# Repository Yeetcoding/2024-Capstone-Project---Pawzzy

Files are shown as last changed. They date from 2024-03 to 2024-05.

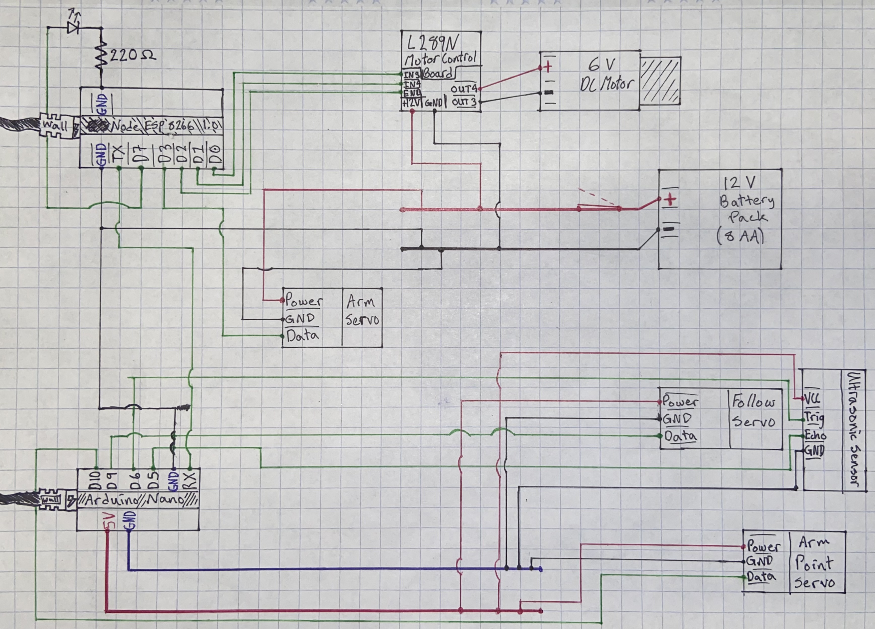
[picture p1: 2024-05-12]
Pawzzy--FINAL_Schematic.jpg

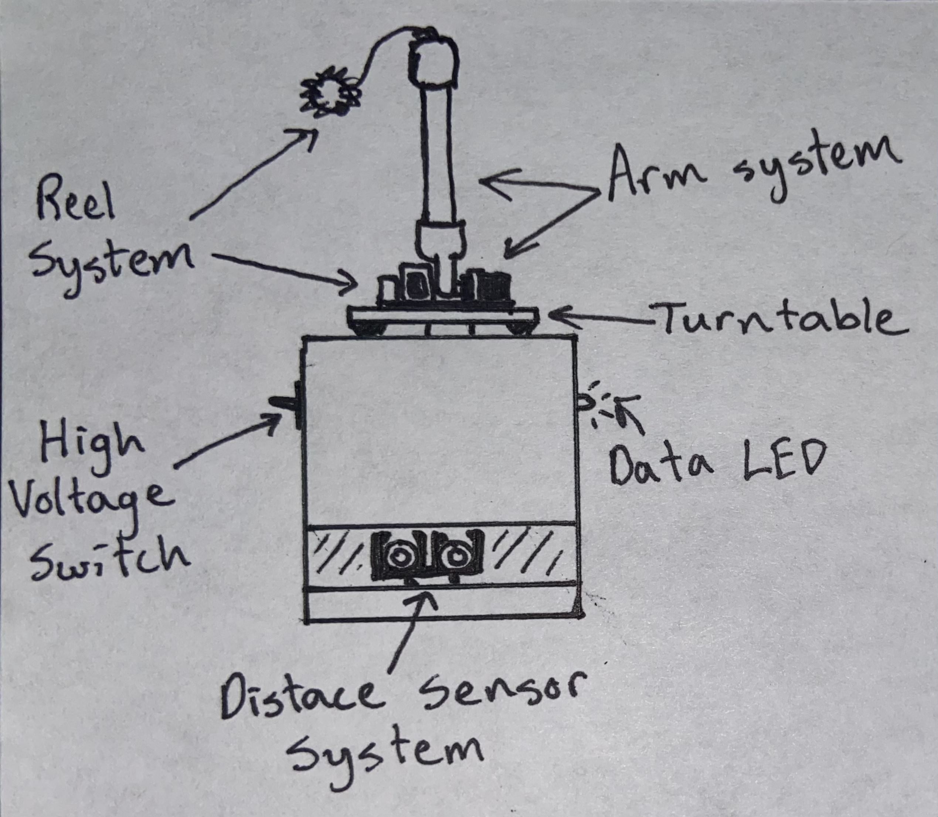
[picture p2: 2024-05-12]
Final_Drawing_Overveiw.jpg

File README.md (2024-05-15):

**2024 Capstone Project**

# **PAWZZY**

2024_05_15_11_23_IMG_0230

**By Chase Smith and Lincoln Willison**

May 15th, 2024

### Project Overview

This robot, named *Pawzzy*, is meant to entertain your cat while you, the owner, are away. One simple tap on your phone, and you don't have to worry about your cat 
feeling lonely! As you would with a cat toy, this machine takes a toy on a string, launches it, and then moves it around for the cat to try to catch. 

As shown in fig.1, the robot has a launch arm, where the toy is attached to moving reel. Like a fishing rod, this arm rotates forward very fast, and the reel is turned on so that the 
toy is launched at a desired distance. 

2024_05_15_11_21_IMG_0229

*Fig. 1*

Then the toy is slowly reeled in as the arm is moved around on the rotating plate, shown in fig.2.

2024_05_15_11_21_IMG_0228

*Fig. 2*

As the toy is being reeled in, the Ultrasonic Sensor at the bottom of the box shown in fig.3 moves close to the direction of the toy, so that if the cat gets close the toy can react and make 
it harder for the cat.

2024_05_15_11_21_IMG_0227

*Fig. 3*

### System Details

The Robot consists of 2 main systems, the Throwing System and a Detection System. As shown in fig.4, the Throwing System consists of the Arm System, The Reel System, and the Turntable, while the Detection System consists of the Distance Sensor and the Servo with it. The Throwing System is responsable for throwing, reeling in, and moving the cat toy, whereas the Detetion System is responsible for detecting the cat and initiating an appropriate response to with the rest of the machine.

Final_Drawing_Overveiw
*Fig.4*

The software for the project is written in Arduino C++, and it used with 2 microcrontrollers, the Node ESP-8266 1.0 and the Arduino Nano. The ESP is used to receive signals from the phone controller of the user and activate the system, as well as control the arm. Fig.5 shows the process and logic implimented in the ESP. 

Pawzzy_FlowC_Transm

*Fig.5*

The Nano is in charge of intaking data from the Detection system and moving the sensor and arm point in the right direction, to help avoid the cat and moce the toy around. Fig.6 shows the process and logic implimented in the Nano, as well as how it makes decisions based on input.

Pawzzy_FlowC_Receiver

*Fig.6*

The Arm Servo is connected to the ESP for control and the 12V battery for power. The Reel Motor is connected to the L289N Motor Control Board, which is controlled by the ESP and is powered by the 12V battery. The LED is connected to the ESP to show the received "ON" signal. The Distance Sensor, Arm Point servo, and Sensor servo are all controlled and powered by the Arduino Nano. Both boards are powered by power cables that plug into an extension cable, which plugs striaght into the wall. The two boards share a Serial connection over the ESP's TX (1) pin, the Nano's RX (0) pin, and a shared ground. All of the electronic wiring is shown on fig. 7. 



*Fig.7*

### Design Evaluation

**Overall Evaluation**

Pawzzy was made to solve two problems: Cat boredom, and the guilt the owner feels when they know their cat has had nothing to do while they're gone. To fufill this goal, we had to make a robot that would be reliable both locally with the randomness of the cat and with the distance of the owner. Our robot has many traits that make it reliable, fun, and beneficial for everyone invovled. We made the robot chassis out of wood to give it a stable and study base. We gave it rubber feet for maximum stability, grip, turn resistence, and so it doesn't scratch any surfaces it is on. We gave it a light blue color of paint to make it visually appealing but also non-threatening. We rounded out the edges of the robot and smoothed over rough surfaces, so that it couldn't hurt anyone or anything brushing against it. Lastly, we use a simply ON/OFF control system for the user, so that the user is only encountered with simplicity and fun times, while the robot does all the hard work. Blynk is a reliable and trusted service that works very fast and reliably, and is very user friendly. 

**Output Display**

For the category Output Display, Pawzzy uses a single LED on the side of the frame to indicate when the robot has received the user's input, as shown in Fig.8. This allows for more understanding of the robot's status to the human, as the human knows that the robot has received the signal to activate. The L298N Motor controller also has an LED to display when power is turned on, but this is hidden from the human since the board is inside the box. 

< insert Fig.8 (LED) here >
*Fig.8*

**Manual User Input**

For the category Manual User Input, Pawzzy uses two different types of input: One through Blynk (shown in Fig.9), where the user presses a digital button to activate the robot, and the other being a physical toggle switch on the side of the frame for controlling the 12V battery. The Blynk input is truly amazing as it allows the user to activate the machine from anywhere with an internet connection, which is perfect for when you are traveling and are away from your cat. At the airport, and want to make sure your cat is not bored? Simply go onto your phone, pressed the "ON" button, and forget about your worries.

< insert Fig.9 (Blynk Screenshots) here >
*Fig.9*
< insert Fig.10 (Toggle Switch) here >
*Fig.10*

**Automatic Sensor**

For the category Automatic Senor, Pawzzy uses an Ultrasonic Sensor, as shown in Fig.11. When combined with a rotating servo, this sensor gives the robot a sense of if the cat is close to the toy. This sensor senses distance, which we use to detect if the cat is close to the toy by closely aligning the senor and the toy. Using this input, the robot is able to move the toy away from the cat by itself, thereby making it harder and more engaging for the cat, as well as introducing more variables to make the moving process more random. 

< insert Fig.11 (Ultrasonic Sensor) here >

**Actuators, Mechanisms, & Hardware**

For the category Actuators, Mechanisms, & Hardware, Pawzzy uses a total of 3 servos and one DC motor, which are all shown in Fig.12. These motors move the arm, move the ultrasonic sensor, and point the arm in the right direction. Each of these motors are aligned and placed so that they fufill their task accordingly, give precise positions, and are not moved under pressure. We use 3d prints for housing and placement, and we use wood for builds like the arm and the box that will be placed under stress, giving it a custom and fitting but rigid design. 

< insert Fig.12 (Servos and Motors) >

**Logic, Processing, and Control**

For the category Logic, Processing, and Control, Pawzzy uses a total of 3 boards, 2 with code in Arduino C++, 1 for controlling power and the DC motor: The Node ESP 8266 1.0, the Arduino Nano, and the L289N, all of which are shown in Fig.13. Since Pawzzy is taking in a contant intake through the ultrasonic sensor and Blynk, it is important that the workload be split between 2 boards, so that one does not get clogged with data and that latency does not get in the way of executing crucial functions at certain times. Our boards are still able to communicate fast and efficiently through the Serial communication pins, where the position for the arm and the Ultrasonic Sensor is dicated by the ESP and received by the Nano, and all systems are able to use data from the others. Because of this two board system, we are able to use the constant input of the Ultrasonic Sensor to react quickly if there is a cat near the toy. The third board, the L289N, allows for us to draw power from a battery that we wouldn't have gotten from the nano or ESP themselves. 

< insert Fig.13 (Boards) >

**Additonal Adjustments**

When designing this, we made sure to do some thinking about how we would put everything together, instead of just throwing it all into a box. We use wood to make a rigid structure, and sand down the edges to make a good and quality feel. We soldered all of the wire joints and components together, so that the internal structure would have a reliable electrical system. We also put thought into the color of our paint - when researching a color that cats like, we found that blue was a common one. We picked our robot to have that blue for its inviting and friendly appeal, so that it would look good to the cat but also the human. We also made sure that the structure and construction of this project would ensure that the different components would work together flawlessly, which it does, as no wires get in the way of the sensor or turntable, and each moving part moves freely without any unecessary friction, and has the suppor that it needs to remain reliable. We are also able to make all of this at a reasonable price, and have no issues with running too close to the budget limit.

Because of the above reasons, we believe we qualify for these additives:
  - +10% for Construction, Quality, Aestetics, and Visual Appeal
  - +10% for Level of Effort
  - +10% for Construction/Production Cost

### Parts List
- Hongwang018 - Acrylic Disk, B0CC83YLVT, $4.50
- MG 996R Servo (x3), $13.50
- Node - ESP 8266 1.0, $5.00
- Arduino Nano, $6.5
- BOJACK - L289N Motor Controller, $3.00
- AEDIKO - DC Motor, $1.40
- Gikfun - Solder Board (x2), $4.4
- Door Hinge, $1.16
- QTEATAK - 8 AA Battery Pack, $3.50
- Plywood, $10
- Marble (x3), $0.30
- EPLZON - Ultrasonic Sensor HC-SR04, $2.00
- Power Strip, $5
- Ace Hardware - Blue paint, $1.8, 
- Ace Hardware - Dowel, $2

### Lessons Learned

- **Beware of the data input from the Ultrasonic Sensor**: During both of our previous capstone projects, we learned how constantly using ultrasonic sensors in a project bog down the time efficiency of the microcontrollers, so we made sure to institute a system that would be able to handle this situation.
- **You can speed up motors with a higher power source but still control it with a microcontroller**: When trying to make the arm servo go faster in order to launch the toy, Chase figured out that if you connect the ground of the Arduino and Power source together and attach the servo's data pin to the Arduino, you can control the servo but it will go significantly faster.
- **Plan out your work schedule and what you are going to make ahead of time**: Both of us have benefited from planning ahead of time what each of us will do with the time we have. In each of our own previous capstone projects, neiter of us planned ahead and barely got work done in time, but this year we were able to work efficiently both as a tem and as individuals because of our planning.
- **Take things step by step**: A concept that is often reiterated throughout all of engineering, it applies also to our situation. The software itself is complex and can get very confusing, so taking it step by step deliberately (especially the very small steps, such as simple Serial communication over a wire or hooking up a servo by itself) and not rushing ahead really helped to make sure all of the "foundations" were sound.
- **Pick a nice color of paint. Make it look 'perty**: Something that we both liked is how well our project looked when we finshed, especially after we put serious thought and effort into what we'd like it to look like. Making it look better, regardless of functionality (but not at the cost of), made us appriciate it more and make it look more friendly and awesome. This was a big difference from our past projects, as our previous projects looked more 'thrown' together than 'put' together.
- **Help others when you can**: Working in a robotics classroom environment like the one in Windosr helps you be around many different people with the same mindset, which means you can have many different opportunities to learn outside/other than the typical lecture to assignment structure. Being able to help others gives you a break from working on your project, gives you a look at other cool projects, and helps you form connections that might pay off later. After all, we know that we appreiciate a helping hand, so why not be that helping hand for another when you can?
- **Don't be a wimp - find a good partner**: Having a good partner changes the game with these capstone projects, as you can get a second view on the project instanly but you can also split the workload with your other partner. Even if you think you can do great yourself, you can do double with a good partner. Both of us chose to go solo with our previous projects, and work together for this one, and the difference is huge because both of us put pour best foot forward and worked hard together. Having a partner is definitely the best choice if you can find a good one. 

### Building Instructions

**If for some reason you've read through all of this and decided you want a crack at making Pawzzy, here are some simple steps to guide you along the way:**
1. Gather Supplies and Parts (parts listed above)
2. Put the Arm Point Servo in the middle of the lid, add on the acrylic cirlce and place all of the top components on the cirlce
3. Wrap all wires in electrical tape, then feed all wires from the top components through the holes in the back of the circle and lid
4. Once all wires are pulled through, solder everything to the appropriate breadboard
5. Attach all physical holders, such as the top assemblies that hold the motors or the dowel ends or the Ultrasonic sensor holder
6. Hot glue all boards and stationary platforms within (but not on the top of) the box to edges of the box
7. Drill 2 holes in opposite sides of the box, one bigger and one smaller
8. Place the High Voltage switch into the bigger of the drilled holes and screw in
9. Glue the LED into the smaller hole 
10. Close the lid of the box, and screw in all top components
11. String through the fishing line and attatch the toy to the end of the line, making sure to pass through all of the loops on the arm
12. Close the box and make sure everything closes fine

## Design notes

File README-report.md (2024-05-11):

**2024 Capstone Project**

# **PAWZZY**

< insert title photo here >

**By Chase Smith and Lincoln Willison**

### Project Overview

This robot, named *Pawzzy*, is meant to entertain your cat while you, the owner, are away. One simple tap on your phone, and you don't have to worry about your cat 
feeling lonely! As you would with a cat toy, this machine takes a toy on a string, launches it, and then moves it around for the cat to try to catch. 

As shown in fig.1, the robot has a launch arm, where the toy is attached to moving reel. Like a fishing rod, this arm rotates forward very fast, and the reel is turned on so that the 
toy is launched at a desired distance. 

< insert fig.1 (launch arm) here >

Then the toy is slowly reeled in as the arm is moved around on the rotating plate, shown in fig.2.

< insert fig.2 (rotating plate) here >

As the toy is being reeled in, the Ultrasonic Sensor at the bottom of the box shown in fig.3 moves close to the direction of the toy, so that if the cat gets close the toy can react and make 
it harder for the cat.

< insert fig.3 (Ultrasonic Sensor) here >

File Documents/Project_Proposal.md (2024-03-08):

2024-Capstone-Project---Pawzzy

Pawzzy

titleImagePawzzy

By Lincoln Willison and Chase Smith

Overview

Pawzzy will be an automated cat entertainment system, designed to eliminate your cat’s boredom while you are gone. The system timing will be determined based on a simple user input in the form of a timer. Once the desired time set by the human is reached, the cat toys will activate. 
	Pawzzy will consist of 4 different systems, The Arm toy, the Laser, the Obstacle Detection System, and the Treat Dispenser, each working together to entice and entertain the cat. The central box, where all of the components will be housed, will be made of either wood, cardboard, or foam with weights on the bottom so that it won't move around during its session.  

Fig 1
fig1_Pawzzy

The Arm Toy will be the main attraction, as it will control the toy that the cat chases. It will be rotated on 2 axes controlled each by a servo motor, so it could move up, down, left, and right, as shown in Fig 2. There will also be a reel controlled by a motor to control the reach of the toy, also shown in Fig 2. This reel will work in function with the arm to cast out the toy like a fishing line, then reel the toy in as the code dictates. The reel motor will also have an encoder, so that when the reel cannot reel in the toy if the cat captures the toy, the Arduino will know and can make decisions based off of that. 

Fig 2
fig2-Pawzzy

The Laser will be a separate system that is also controlled by two servos. The laser will be mounted on the two servos and point to various spots on the ground, as shown in Fig 3.

Fig 3
fig3-Pawzzy

The Obstacle detection system will be composed of an ultrasonic sensor and a servo. The servo will move the sensor in a semicircle, and the data collected from the sensor will be inputted into the Arduino. We have not yet determined where the sensor will be on the body, as the answer is better decided on testing.
The Treat Dispenser will dispense treats based on what happens to the toy, and how many treats the cat has already gotten. It will be controlled by a servo.  

Fig 4
fig4-Pawzzy

Components:

________________________________
Key:
Red: Output Display
Blue: Manual User Input
Orange: Automatic Sensor
Green: Actuators, Mechanisms and Hardware
Yellow: Logic, Processing, and Control
_____________________________________

Arduino Mega - to provide and execute the code of the project
Laser Diode - to make a laser that the cat chases
Wood/foam/cardboard - for the structure of the box
3d Print Filament - for the arm, spool, internal and external structure
6 small servo motors - 2 for the Arm, 2 for the laser, one for the distance sensor, and 1 for the treat dispenser
Small DC motor with encoder - for controlling the string attached to the arm and knowing when the cat has captured the toy
Buttons - for time input and input from the cat
LED’s - indicators for the working status of the machine, mode, and if toy has been captured
Ultrasonic Sensor - for sensing objects that might obstruct the toy throws
Buzzer - to signal accepted inputs (ei. Timer button pressed), signaling the capture of the toy, and the dispense of a treat

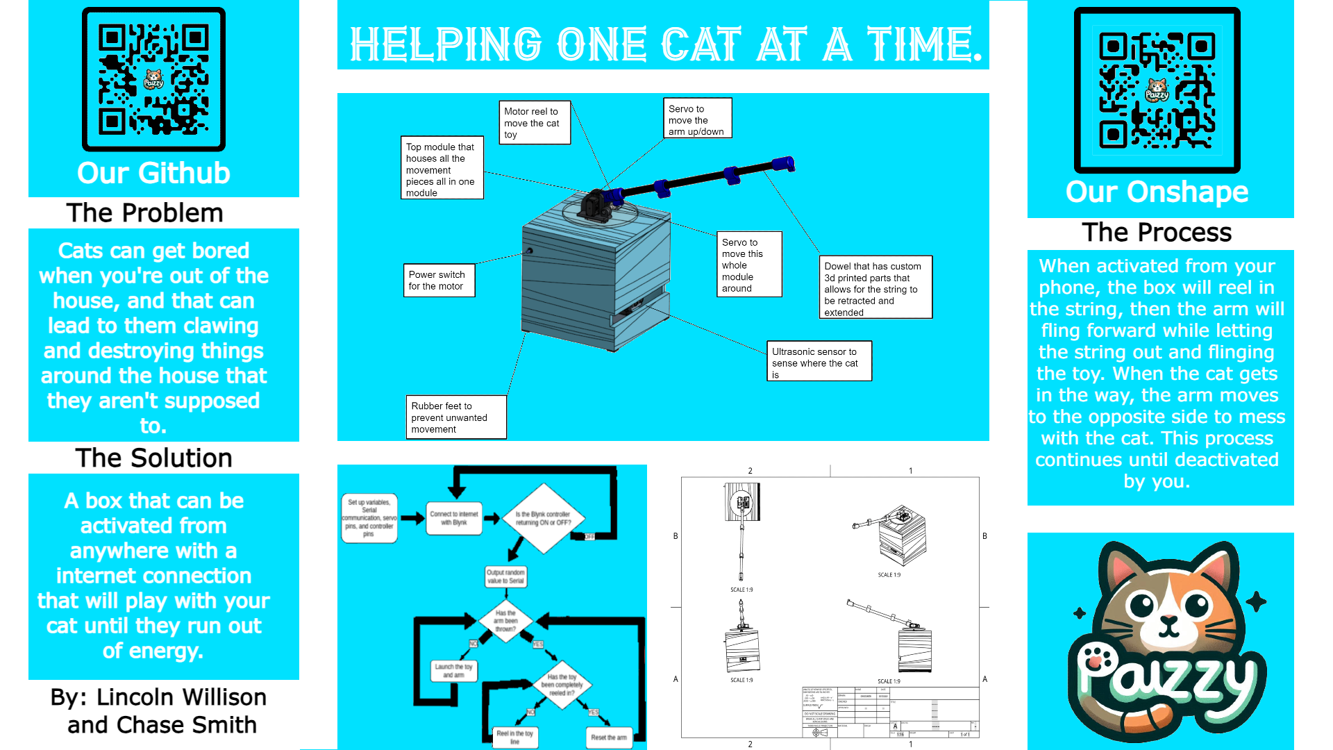
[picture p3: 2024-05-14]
Pawzzy_Poster.png

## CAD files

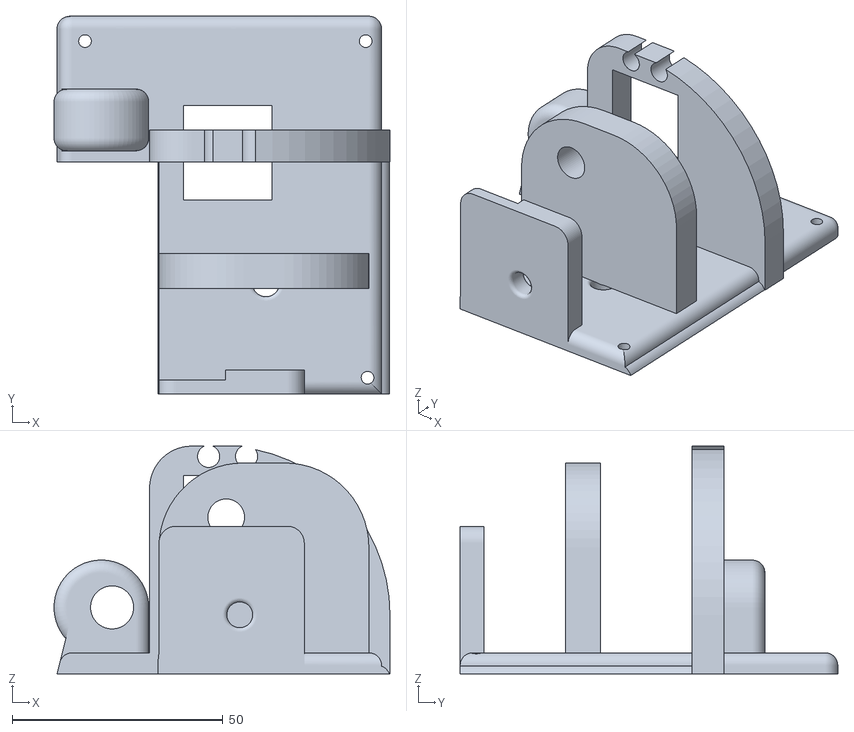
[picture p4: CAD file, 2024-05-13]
3D_Files/Top module (5).stl
79.7 x 89.5 x 54.0

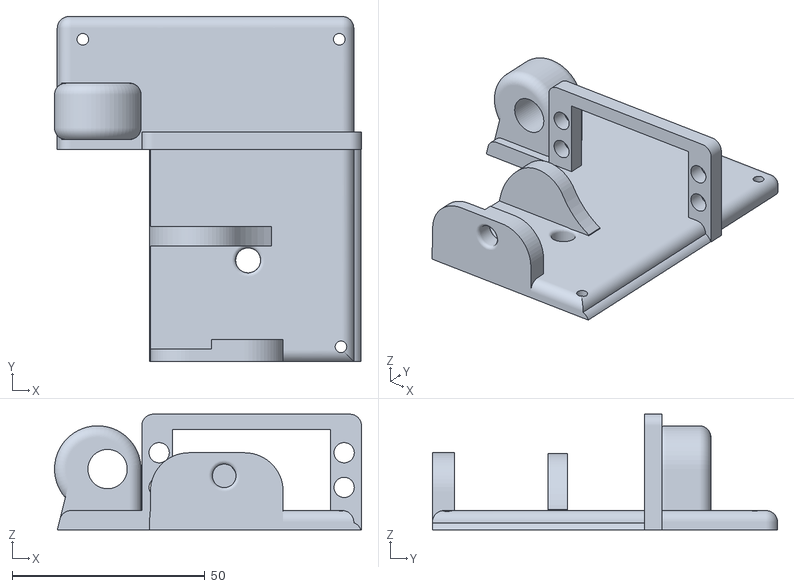
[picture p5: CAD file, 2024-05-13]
3D_Files/Top module (3).stl
79.7 x 89.5 x 30.0

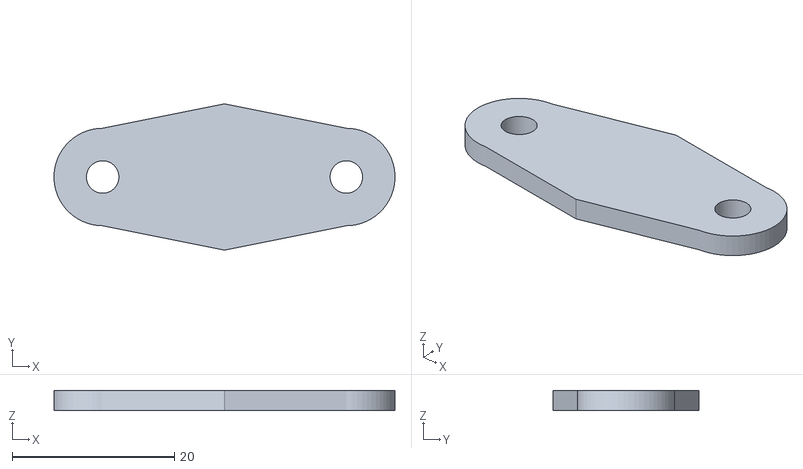
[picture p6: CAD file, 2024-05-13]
3D_Files/Marble roller spacer (2).stl
42.0 x 18.0 x 2.50

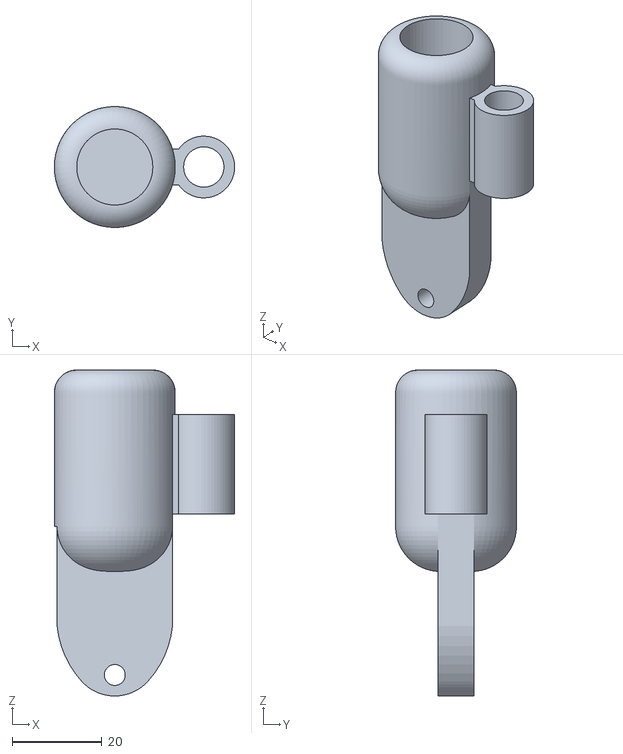
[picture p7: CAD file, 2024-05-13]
3D_Files/Dowel end (2).stl
40.3 x 27.0 x 72.8

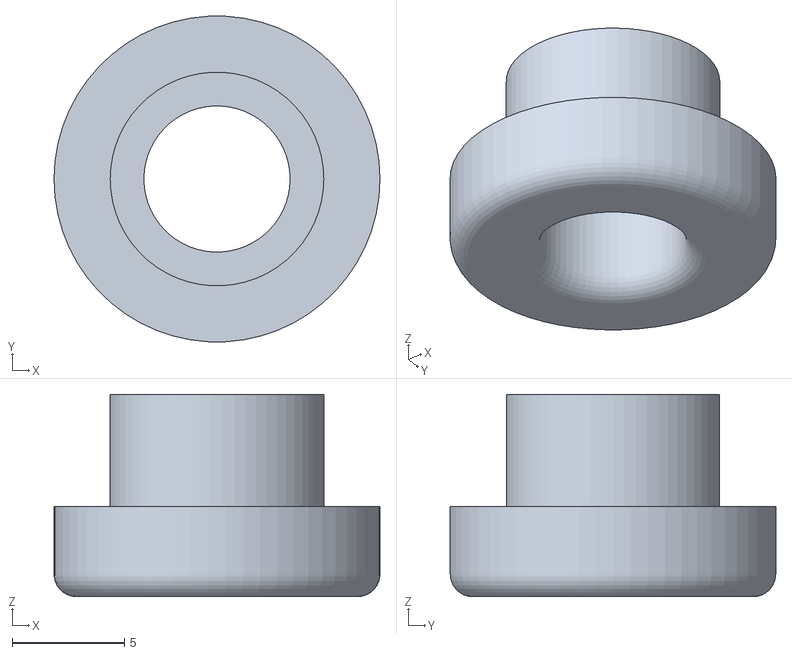
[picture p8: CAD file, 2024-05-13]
3D_Files/Cable insert (3).stl
14.5 x 14.5 x 9.00

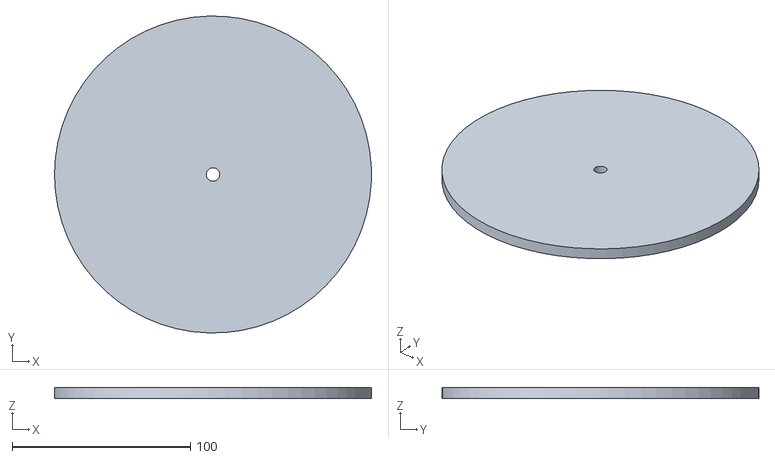
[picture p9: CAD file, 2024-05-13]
3D_Files/Turn table (1).stl
177.8 x 177.7 x 6.35

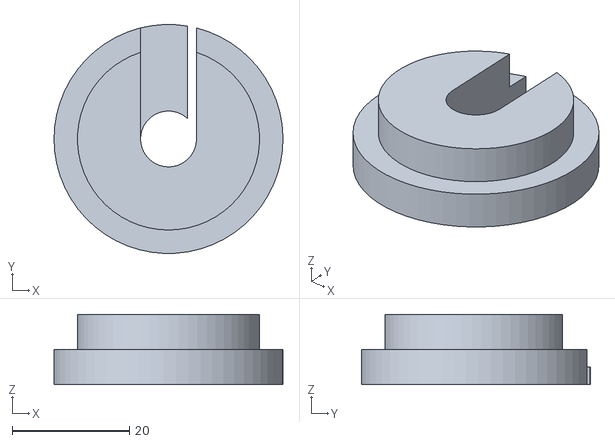
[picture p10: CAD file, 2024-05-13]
3D_Files/Power cord cover.stl
39.0 x 39.0 x 12.0

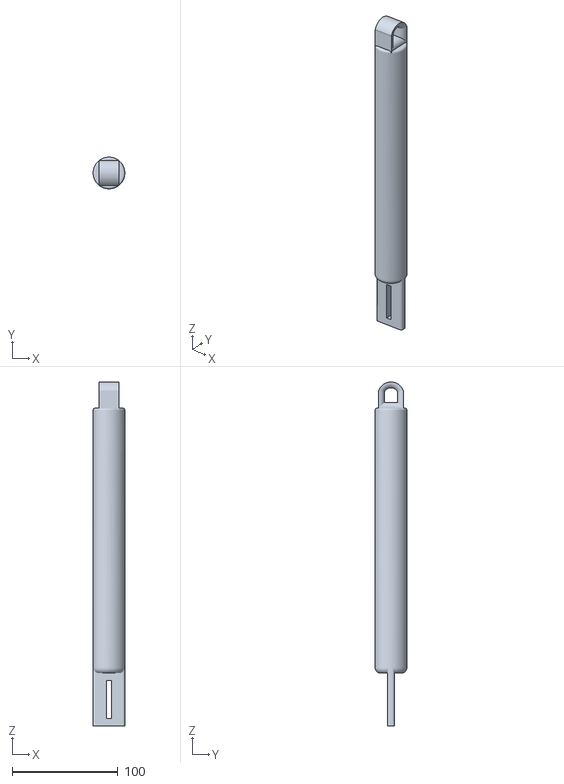
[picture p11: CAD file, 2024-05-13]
3D_Files/Throwing arm.stl
30.0 x 30.0 x 324.6

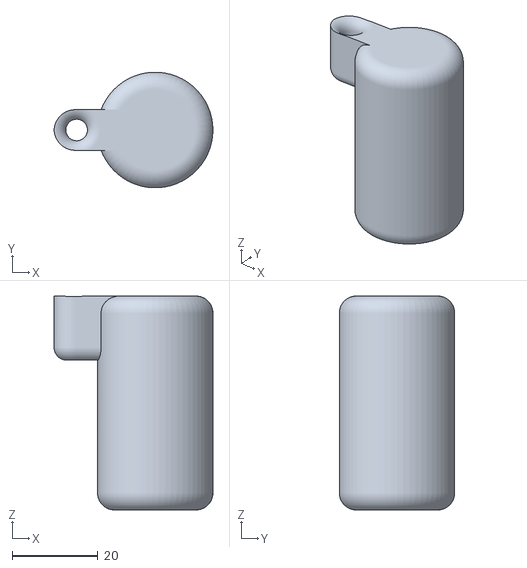
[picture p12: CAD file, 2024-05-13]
3D_Files/Other dowel end (1).stl
37.1 x 27.0 x 50.0

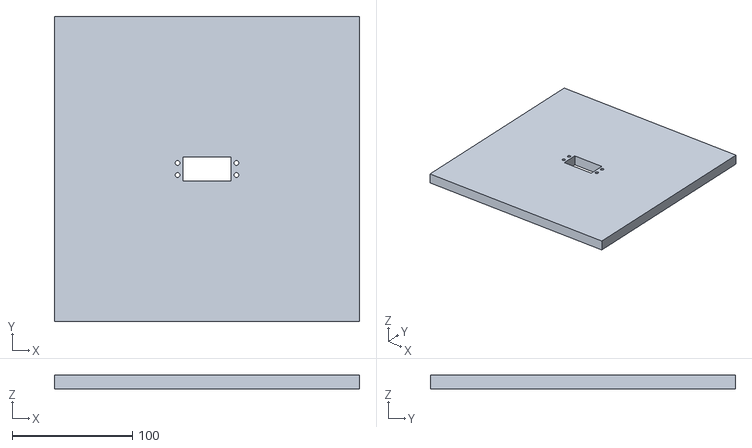
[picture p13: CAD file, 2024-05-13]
3D_Files/Lid.stl
254.0 x 254.0 x 12.0

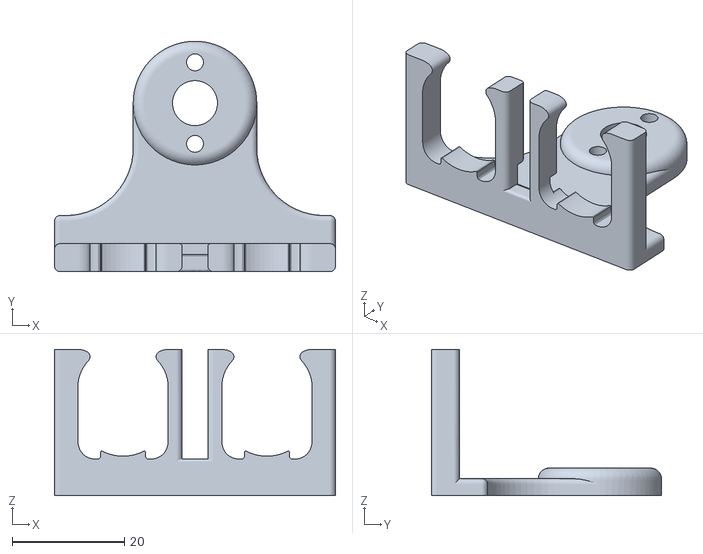
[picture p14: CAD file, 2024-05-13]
3D_Files/Ultra-sonic sensor holder (2).stl
50.0 x 41.0 x 26.0

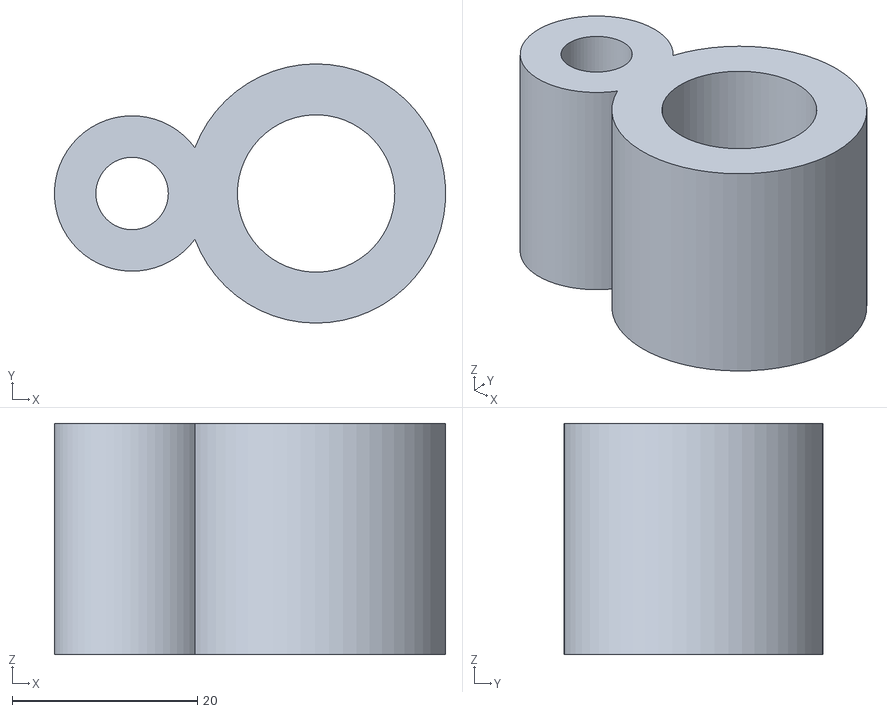
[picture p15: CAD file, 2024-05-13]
3D_Files/String retainer (1).stl
42.2 x 28.0 x 25.0

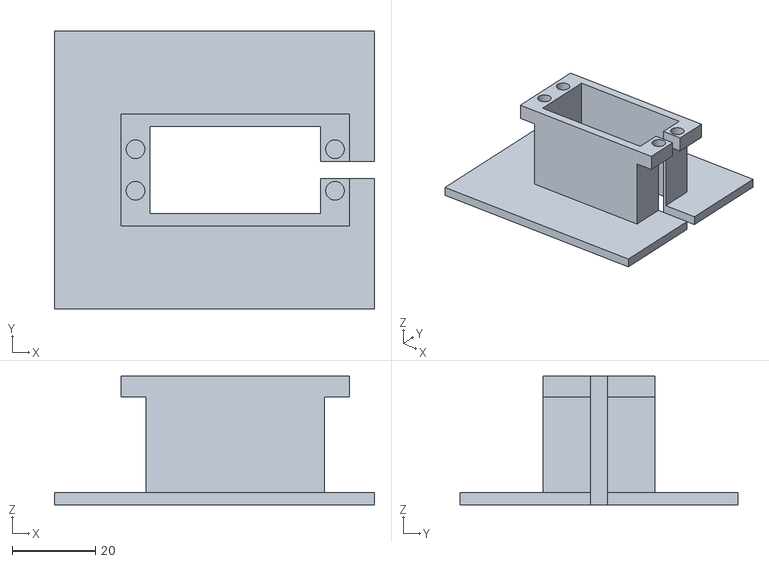
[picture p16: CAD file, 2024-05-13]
3D_Files/Ultrasonic sensor servo mount (2).stl
77.0 x 67.0 x 31.0

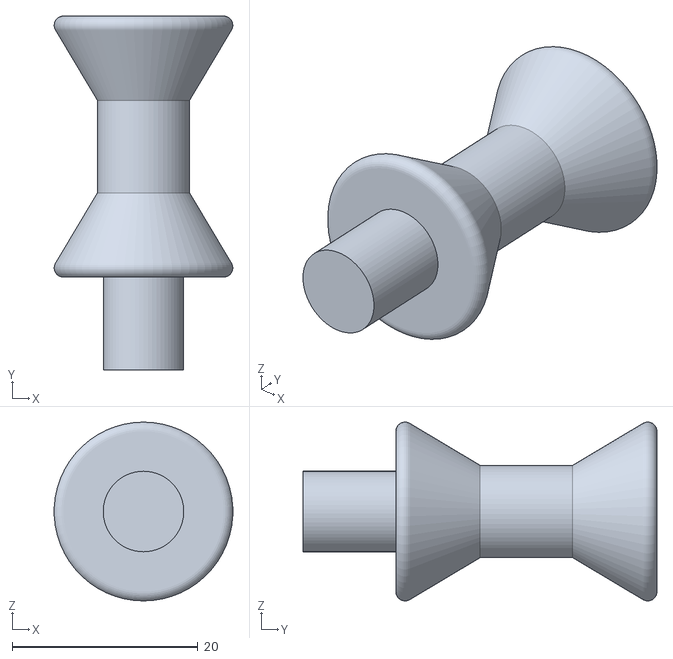
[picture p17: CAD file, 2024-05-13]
3D_Files/Spool (2).stl
19.2 x 38.1 x 19.3

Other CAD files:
3D_Files/rubber feet.stl
3D_Files/Box.stl
3D_Files/dowel.stl

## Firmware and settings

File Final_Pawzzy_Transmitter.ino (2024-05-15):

// Creates Identification for the Blynk system
#define BLYNK_TEMPLATE_ID "TMPL2SN2Sv__H"
#define BLYNK_TEMPLATE_NAME "PawzzyESP"
#define BLYNK_AUTH_TOKEN "Q0CI0nawhmAF8260h05qQLF5BY6Zh9Hb"

// Includes all necessary libraries
#include <ESP8266WiFi.h>
#include <BlynkSimpleEsp8266.h>
#include <Servo.h>

// Creates the name and password of the network the ESP needs to connect to
char ssid[] = "mechlab";
char pass[] = "etufh89959"; 

bool blynk_input = false; // bool for user input
bool arm_throw = false; // bool for knowing if the arm has thrown the toy or not

int blynk_input_LED = D7; // int for the output LED pin
int arm_pos = 90; // int for the position of the arm 
int arm_point_pos = 90; // int for the transmitted number used to determine direction of the arm
int move_time = 500; // int for determining how long the reel will move for (hence how long to drop the toy for)

Servo arm; // Sets up the Arm servo

void setup(){
  Blynk.begin(BLYNK_AUTH_TOKEN, ssid, pass); // Connects ESP to Internet
  Serial.begin(115200); // Sets up Serial communication

  pinMode(blynk_input_LED,OUTPUT); // Sets up LED 
  
  // Sets up control pins leading to the L289N board
  pinMode(D0,OUTPUT);
  pinMode(D1,OUTPUT);
  pinMode(D2,OUTPUT);
  
  arm.attach(D3); // Sets up servo to pin D3
  arm.write(100); // Sets up a starting position
}

// Function based off of Blynk input
BLYNK_WRITE(V0){
  int i = param.asInt(); // local variable to check status of input
  
  // If user turns on button, light up LED and change bool to TRUE
  if (i == 1){
    digitalWrite(blynk_input_LED, HIGH);
    blynk_input = true; 
  }
  // Otherwise, turn off LED and set bool to FALSE
  else{
    digitalWrite(blynk_input_LED, LOW);
    blynk_input = false;
  }
}

// Function to set the toy in the down position
void reel_down(){
  digitalWrite(D0,HIGH);
  digitalWrite(D1,LOW);
  analogWrite(D2,255);
  return;
}

// Function to recall the toy to the top if the setup needs to be repeated
void reel_up(){
  digitalWrite(D0,LOW);
  digitalWrite(D1,HIGH);
  analogWrite(D2,255);
  return;
}

// Function for turning off the motor when called
void reel_off(){
  digitalWrite(D0,LOW);
  digitalWrite(D1,LOW);
  analogWrite(D2,0);
  return; // Stop/check function
}

void loop(){
  Blynk.run(); // Run all Blynk functions (connecting to internet, checking data)

  // If the user turns on the button then do this:
  if (blynk_input == true){
    // If the arm hasn't been set, move into position and lower toy
    if (arm_throw == false){
      arm.write(180);
      reel_down();
      delay(500);
      reel_off();
      arm_throw = true;
    }
    // Otherwise, move the toy around  
    else{
      arm_point_pos = random(60,121);
      Serial.write(arm_point_pos);
    }
    
  }
  // Otherwise (being the user has not pressed the digital button), turn the reel off and don't move
  else{
    reel_off();
    Serial.write(20);
  }
}

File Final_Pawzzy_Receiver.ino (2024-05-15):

#include <Servo.h> // Includes the servo library

// Sets pins for the ultrasonic sensor
#define echoPin 5 
#define trigPin 6

// Sets the servos to their correct pins
Servo followSensor; 
Servo armPoint;

int serialInput = 90; // Int for reading Serial input
int distance; // Int for reading distance input from the sensor
int react_counter = 2; // Int for position calculations

long duration; // Used to calculate distance using input from the sensor

void setup() {
  Serial.begin(115200); // Sets Serial communication to correct speed

  pinMode(13,OUTPUT); // LED output pin
  pinMode(trigPin, OUTPUT); // Trig pin for sensor
  pinMode(echoPin, INPUT); // Echo pin for sensor
  
  followSensor.attach(9); // Pin for directing the servo that turns the sensor
  armPoint.attach(10); // Pin for directing where the arm points and how the turntable turns

  // Setting starting positions
  followSensor.write(90);
  armPoint.write(90);

}

// Function used to find distance from sensor
void ult(){
  digitalWrite(trigPin, LOW);
  delayMicroseconds(2);
  digitalWrite(trigPin, HIGH);
  delayMicroseconds(10);
  digitalWrite(trigPin, LOW);
  duration = pulseIn(echoPin, HIGH);
  distance = duration * 0.034 / 2;
}

void loop() {
  ult(); // Activate the ultrasonic sensor

  // If distance is less than 35, either go way to the left or way to the right depending on where you went last
  if (distance < 35){
    react_counter += 1;
    if (react_counter % 2 == 0){
      followSensor.write(60);
      armPoint.write(60);
    }
    else{
      followSensor.write(120);
      armPoint.write(120);
    }
  }
  // If no cat is detected, set the arm point and sensor to point at the received input number
  else {
    serialInput = Serial.read();
    
    if (serialInput != 20 and serialInput != -1 and serialInput != 1){
      followSensor.write(serialInput);
      armPoint.write(serialInput);
    }
    else if (serialInput == 20 or serialInput == -1 or serialInput == 1){
      digitalWrite(13,LOW);
    }
  }
}
